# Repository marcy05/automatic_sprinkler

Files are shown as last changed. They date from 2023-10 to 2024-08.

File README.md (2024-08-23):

# Automatic Sprinkler
The project is intended to let your plant to survive while you are on holiday and you do not have any intention to buy built-in mechanism that prevent you to expand and adjust the system to your needs.

If you find this project it means that you are going to build it :)

# Getting started

## Folder Structure

The Repository is structure so that:

|Folder|Content description|
|-|-|
|/3d_files|It contans all the stl files that you need to print for the project.|
|/Board|It contains the reference schematics of the PCB|
|/Board/Production/|It contains the different files for fabrication or editing|
|/SourceCode|It contains all the developend source code|
|/SourceCode/src/ + sprinkler.py|It is the code needed for the Raspberry Pi Pico W to control the PCB board. The *src* folder has to be uploaded on the microcontroller while the *sprinkerl.py* can be executed locally for tests or uploaded on the target as well.|
|/SourceCode/Scripts/|It contains some tests that can be executed to test the wiring.|

## Bill of Material for the PCB and water buffer.

|Item #|Description|Quantity|Cost ~€/piece|Reference|
|-|-|-|-|-|
|1|Raspberry Pi Pico w|1|5,08|[Link](https://www.kubii.com/it/le-schede-raspberry-pi/3205-raspberry-pi-pico-w-h-wh-3272496311589.html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)|
|2|Multiplexer analogico CD74HC4067|2|1,30|[Link](https://www.amazon.it/gp/product/B09B4213T3/ref=ox_sc_act_title_1?smid=A2ETWJBO4PH7XN&psc=1)|
|3|Relay 3V with Optocoupler|7|3,60|[Link](https://www.amazon.it/gp/product/B07PLQNSW2/ref=ppx_yo_dt_b_search_asin_title?ie=UTF8&psc=1)|
|4|Buck converter|1|2,20|[Link](https://www.amazon.it/gp/product/B0B4S3T48P/ref=ewc_pr_img_1?smid=A1RRESHOTNJOS4&psc=1)|
|5|JST-XH 2,54mm 3pin|7|n/a|[Link](https://www.amazon.it/gp/product/B07RP6876C/ref=ppx_yo_dt_b_search_asin_title?ie=UTF8&psc=1)|
|6|JST-XH 2,54mm 2pin|7|n/a|[Link](https://www.amazon.it/gp/product/B07RP6876C/ref=ppx_yo_dt_b_search_asin_title?ie=UTF8&psc=1)|
|7|Diode IN4001|7|n/a|[Link](https://www.amazon.it/gp/product/B07Q8RPBVY/ref=ppx_yo_dt_b_search_asin_title?ie=UTF8&psc=1)|
|8|Mini water pumps 3V/5V|7|2,20|[Link](https://www.amazon.it/dp/B09Z28NFT3?psc=1&ref=ppx_yo2ov_dt_b_product_details)|
|9|Pin header connector female|Some|10|[Link](https://www.amazon.it/Headers-Breakaway-Connector-Prototype-intestazione/dp/B07CC4V9ZY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)|
|10|DC connector DC-0055.5x2.1mm|1|0,10|[Link](https://it.aliexpress.com/item/1005001688314286.html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)|
|11|Power supply 5V 2A|1|7,00|[Link](https://www.amazon.it/gp/product/B09DSWL12H/ref=ewc_pr_img_1?smid=A1LPCHZ6DX1HO3&psc=1)|
|12|Power switch 5V|1|n/a|[Link](https://www.amazon.it/gp/product/B07J4KB38W/ref=ewc_pr_img_1?smid=A3BZ3PT9ZR43MC&psc=1)|
|13|(optional) Led green|2|n/a|[Link](https://www.amazon.it/gp/product/B07DPJ23YT/ref=ewc_pr_img_1?smid=A3BZ3PT9ZR43MC&psc=1)|
|14|(optional) Box case|1|n/a|[3d_file](3d_files/case_half1.STL)|
|15|(optional) Box case cover|1|n/a|[3d_file](3d_files/case_half2.STL)|
|16|Water frame buffer|1|n/a|[3d_file](3d_files/frame_buffer.STL)|
|17|Water frame buffer top|1|n/a|[3d_file](3d_files/frame_buffer_top.STL)|
|18|Pump holders|2|n/a|[3d_file](3d_files/pump_buffer.STL)|
|19|Holder top|2|n/a|[3d_file](3d_files/holder_top.STL)|
|20|Relay support|2|n/a|[3d_file](3d_files/support_relay.STL)|
|21|(optional) PCB to be printed|1|n/a|[PCB](Board/Schematic_Automatic_Sprinkler_2023-07-30.pdf)|
|22|Empty tank sensor|1|n/a|[Link](https://www.amazon.it/dp/B0B7S2N6B3?ref=ppx_yo2ov_dt_b_product_details&th=1)|

## Software

The file must be named ***main.py*** in order to be executed directly at the start-up of the shield.

## How to start to test the softwarre

* Copy the */src* folder that you find the SourceCode folder to your Raspberry Pico W

* Copy / execute the file *sprinkler.py* . If you want that it will be executed automatically at the startup you have to copy the file *sprinkler.py* to Raspberry Pico and rename it as *main.py*

## What to do to start

1. Copy the source files in Raspberry Pi Pico W (/src + sprinkler.py)

2. Rename my_secret.py.template to my_secret.py

3. Edit my_secret.py adding:

    * Your network information (SSID, password)

    * Create a telegram bot:

        * On Telegram, search @ BotFather, send him a “/start” message

        * Send another “/newbot” message, then follow the instructions to setup a name and a username

        * Your bot is now ready, be sure to save a backup of your API token, and correct, this API token is your bot_token
    
    * Add the API token in the file

    * Save the file

4. You can now run the code

5. On Telegram, search your bot (by the username you just created), press the “Start” button or send a “/start” message

# Changelog

## V2.2.2

* Add broadcasted messages

## v2.2.1

* Add tank full control before each pump activation

## v2.2.0

* Removed direct pump activation via telegram causing issues

* Add new attribute to set back the flags for daily watering (daily_watering_done) via _watering_day

* Add new cycle to reset flags for daily watering

* Add new telegram messages for a better control on the variables in the running system

## v2.1.1

* Add support for external LEDs for RUN and WiFi

## v2.1.0

* Renamed main file for auto execution

* Add status led when running

* Set watering period to 1 day, dev 50s commented out

* Fix missing return False in is_evening

* Add flow diagrams

## v2.0.0

* First release implementing telegram controlled automatic sprinkler

* User authentication

* 7 autonomous pumps

* 7 autonomous sensors

* Automatic watering cycle

* Manual watering cycle

* Pump activation time with persistency parameters controlled remotelly

* Pump activation and deactivation with persistency and remote contol

* Emergency system stop via remote message

## v1.0.1

## v1.0.0

# Licence

Please check the dedicated file in *main* branch.

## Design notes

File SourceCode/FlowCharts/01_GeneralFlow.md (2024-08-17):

@startuml

title 01 Sprinkler General Flow

:Create HwInterface object
to reset all mux;

:Define Garden object my_garden
* Init Backend
* Init timers;

:Turn on status led;

repeat
    :my_garden.run();
repeat while (Forced exit from telegram?) is (yes)
    :Log event;
    :Reset all mux;
stop

@enduml

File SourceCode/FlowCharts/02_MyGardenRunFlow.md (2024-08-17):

@startuml

title 02 Garden Run Flow

start

if (is_tank_full() ?) then (yes)

    note right
    is_tank_full() just read the PIN 28,
    if < 3V it returns False.
    end note

    :pump_deactivation_sem = True;

    if (is_watering_moment() ?) then (yes)
        :pump_cycle();
        :watering_timer = current time;
    endif

else (no)
    if (pump_deactivation_sem) then (yes)
        :deactivate_all_pumps();
    endif

endif

if (is_sensor_reading_moment() ?) then (yes)
    :reading_sensors();
    :set sensor_reading_timer;
endif

if (is_log_moment() ?) then (yes)
    :run garbage collector;
    :log system alive;
    :get evaluate_data_from_telegram();
    if (tg answer == ForcedExit) then (yes)
        :retun "ForcedExit";
        stop
    else (no)
    endif
else (no)
endif

end

:is_watering_moment;

if (daily_watering_done) then (no)
    if (now - watering_timer >= watering_period) then (yes)
        if (NTP time sync done) then (yes)
            if (is_evening) then (yes)
                :daily_watering_done = True;
                :return True;
                stop
            else (no)
                :return False;
                stop
            endif
        else (no)
            :log NTP not sync;
            :daily_watering_done = True;
            :return True;
            stop
        endif
    else (no)
        :return False;
        stop
    endif
else (no)
    :return False;
    stop
endif

:is_evening;
: get time and date;
if (Jan, Feb, Mar, Apr, May, Oct, Nov, Dec) then (yes)
    if (current hour >= 18) then (yes)
        :retun True;
        stop
    else (no)
    endif
else (no)
endif

if (May, Jun; Jul, Sep) then (yes)
    if (current hour >= 19) then (yes)
        :return True;
        stop
    else (no)
    endif
else (no)
endif

:return False;

end

:evaluate_data_from_telegram(self);
:t_msg = telegram.read_once();

if (t_msg not None) then (yes)
    if (t_msg == "/system_stop") then (yes)
        :return ForcedExit;
        stop
    else (no)
    endif

    if (t_msg == "<general message>") then (yes)
        :<general implementation>;
        note
        The implementation depends on
        the message selected
    end note
        stop
    else (no)
    endif

else (no)
    :log no new messages;
endif

end

:pump_cycle();

repeat :for iteration in watering_iterations;
    repeat :for pump in pumps;
        if (pump get_active_status()) then (yes)
            :pump watering();
        else (no)
            :log inactive pump;
            note right
                This pump will be skipped
            end note
        endif
    repeat while (more pump?) is (yes)

repeat while (more iteration? ) is (yes)

end

@enduml

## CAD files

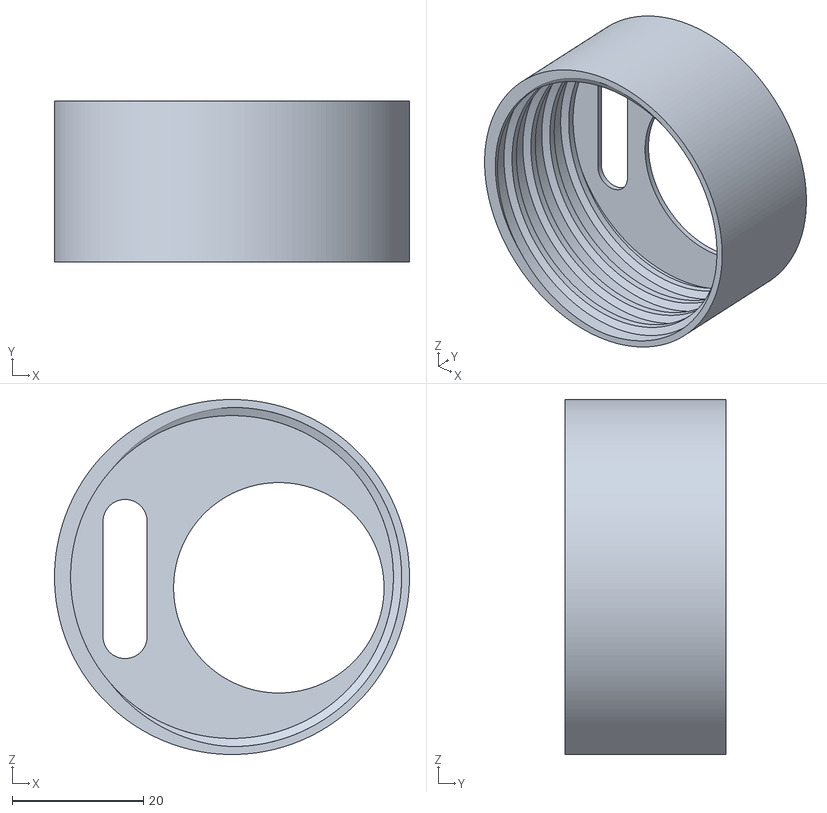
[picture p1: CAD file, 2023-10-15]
3d_files/tank_cap.STL
54.0 x 24.5 x 54.0

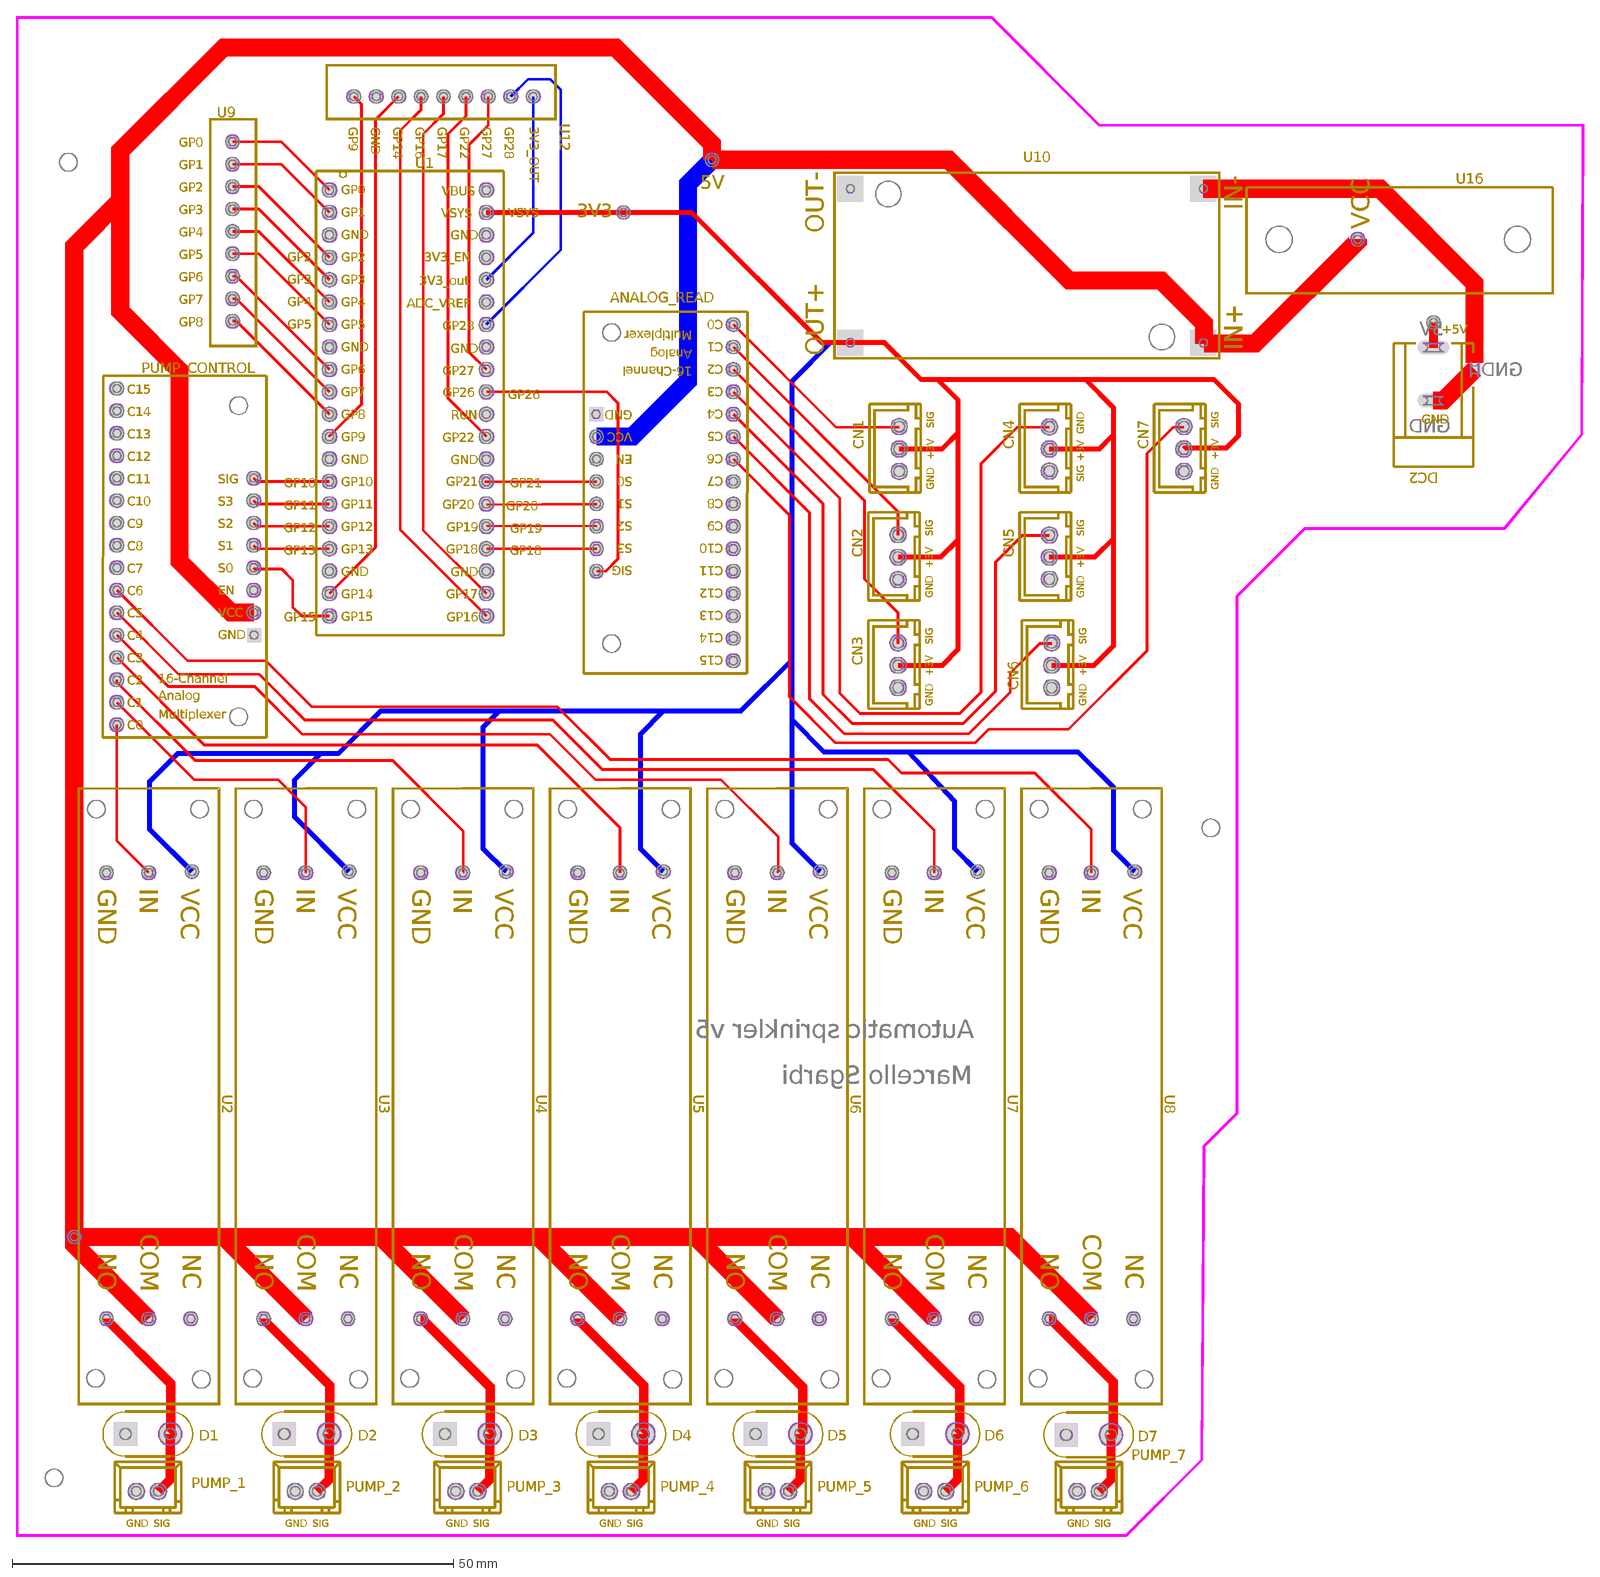
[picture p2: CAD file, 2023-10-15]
Board/Production/PCB_Irrigatore_01_2023-07-30.dxf
Automatic sprinkler v5
Marcello Sgarbi
5V
GND
+5V
3V3
GP5
GP4
GP3
GP2
GP10
GP11
GP12
GP13
GP15
GP20
GP21
GP19
GP18
GP26
VSYS
CN1
+3V
SIG
CN2
CN3
CN6
CN7
U9
GP8
GP7
GP6
GP1
GP0
U12
3V3_OUT
GP28
GP27
GP22
GP17
GP16
GP14
GP9
U16
VCC
D1
D2
D3
D4
D5
D6
D7
U10
IN+
IN-
OUT+
OUT-
DC2
CN5
CN4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

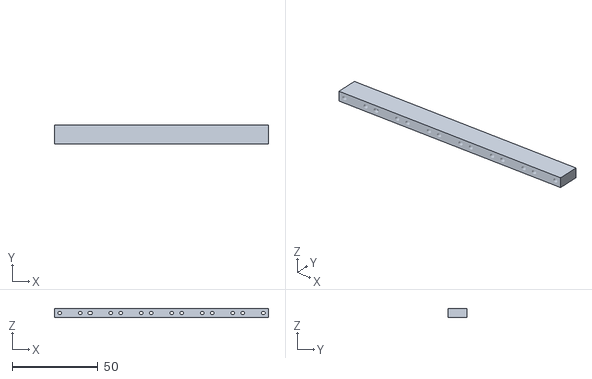
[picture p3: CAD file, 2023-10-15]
3d_files/support_relay.STL
124.8 x 11.1 x 5.00

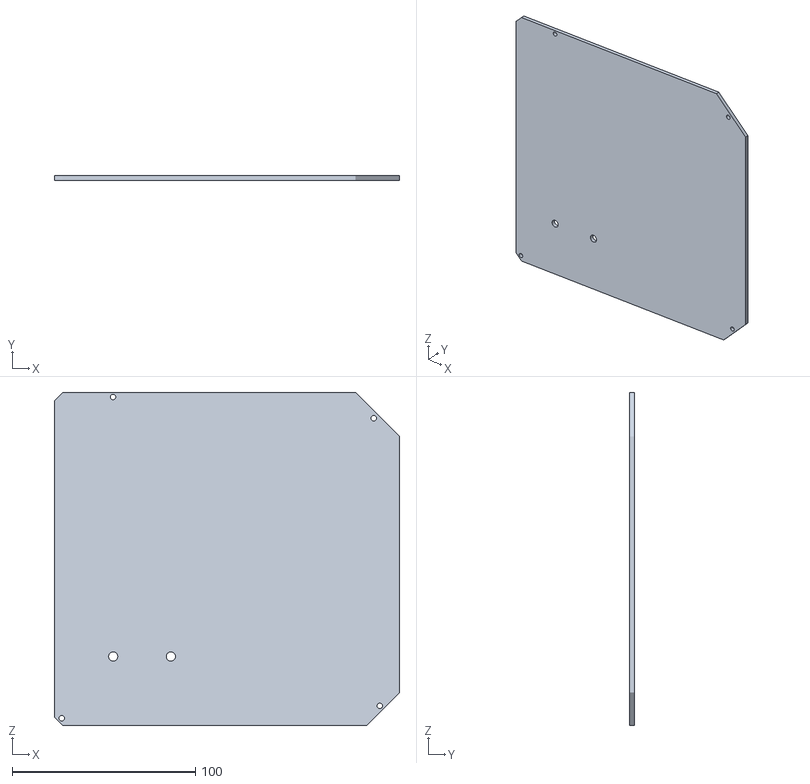
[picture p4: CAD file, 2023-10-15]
3d_files/case_half2.STL
188.4 x 2.50 x 181.9

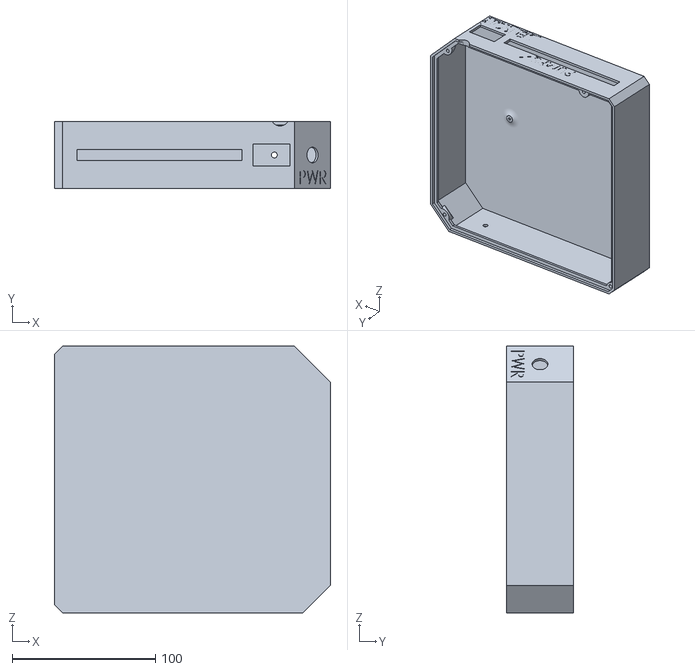
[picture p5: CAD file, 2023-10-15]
3d_files/case_half1.STL
192.4 x 47.0 x 185.9

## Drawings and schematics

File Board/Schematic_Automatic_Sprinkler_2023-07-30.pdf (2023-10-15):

## INPUT DC-DC CONVERTER LOGIC

## Extra Pins

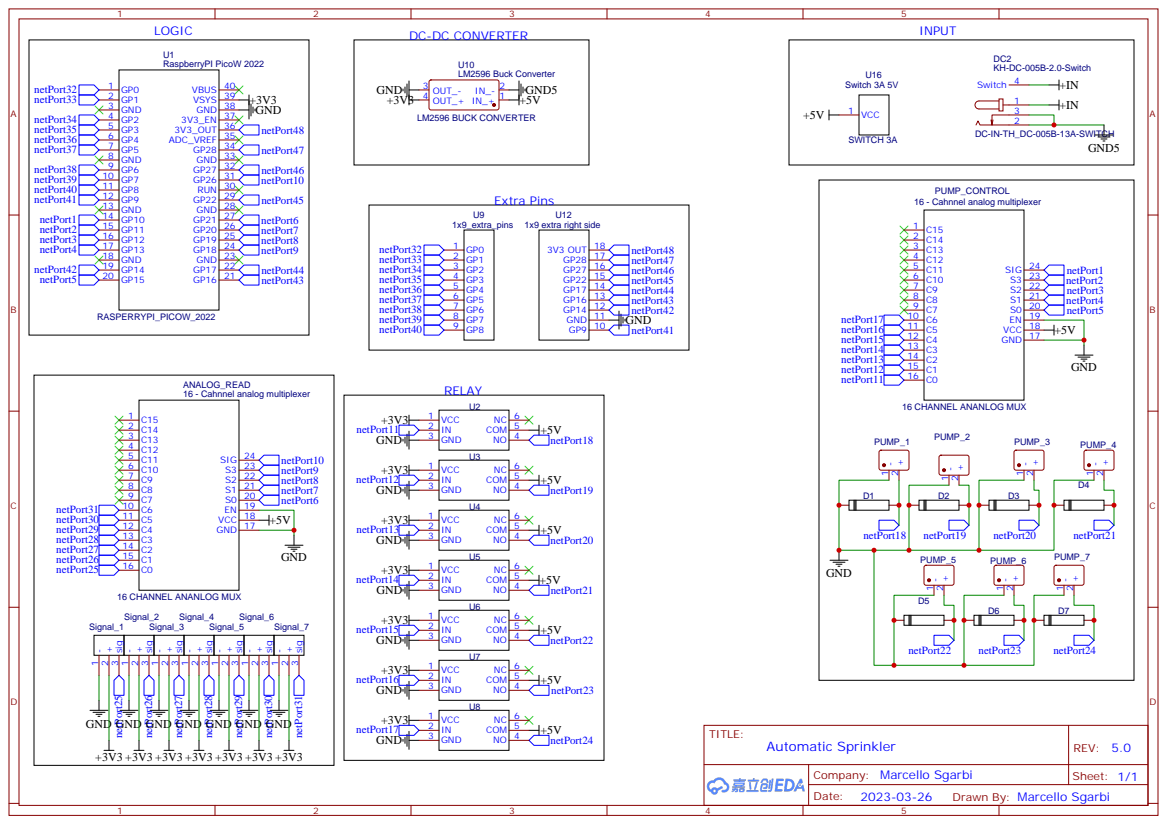
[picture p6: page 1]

ANALOG_READ
16 - Cahnnel analog multiplexer
GND 17 VCC 18 EN 19 S0 20 S1 21 S2 22 S3 23 SIG 24

netPort26
GND GND GND

Drawn By: Marcello Sgarbi

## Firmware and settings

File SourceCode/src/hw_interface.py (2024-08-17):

# #############################################################################
#                               IMPORT
# #############################################################################
import os
import utime
import machine

from src.simple_logger import logger
from src.persistencyHandler import get_persisted_timers
from src.persistencyHandler import write_persistency_value
from src.persistencyHandler import get_pump_active_status, write_pump_active_staus
from src.utils_func import bool2onoff

# #############################################################################
#                          GLOBAL VARIABLES
# #############################################################################

status_led = machine.Pin("LED", machine.Pin.OUT)
status_led.value(0)

status_led_ext = machine.Pin(9, machine.Pin.OUT)
status_led_ext.value(0)

status_led_wifi = machine.Pin(14, machine.Pin.OUT)
status_led_wifi.value(0)

# #############################################################################
#                               CLASSES
# #############################################################################

class HwInterface:
    def __init__(self) -> None:
        self.mux_channels_used = 7

        self.__pump_sig = 10
        self.__pump_s3 = 11
        self.__pump_s2 = 12
        self.__pump_s1 = 13
        self.__pump_s0 = 15

        self.__sensor_sig = 26
        self.__sensor_s3 = 18
        self.__sensor_s2 = 19
        self.__sensor_s1 = 20
        self.__sensor_s0 = 21

        self.__water_level = 28

        self.d_s0 = machine.Pin(self.__pump_s0, machine.Pin.OUT)
        self.d_s1 = machine.Pin(self.__pump_s1, machine.Pin.OUT)
        self.d_s2 = machine.Pin(self.__pump_s2, machine.Pin.OUT)
        self.d_s3 = machine.Pin(self.__pump_s3, machine.Pin.OUT)
        self.d_sig = machine.Pin(self.__pump_sig, machine.Pin.OUT)

        self.a_s0 = machine.Pin(self.__sensor_s0, machine.Pin.OUT)
        self.a_s1 = machine.Pin(self.__sensor_s1, machine.Pin.OUT)
        self.a_s2 = machine.Pin(self.__sensor_s2, machine.Pin.OUT)
        self.a_s3 = machine.Pin(self.__sensor_s3, machine.Pin.OUT)
        self.a_sig = machine.ADC(self.__sensor_sig)

        self.multiplex_selector = [(0, 0, 0, 0),
                                   (1, 0, 0, 0),
                                   (0, 1, 0, 0),
                                   (1, 1, 0, 0),
                                   (0, 0, 1, 0),
                                   (1, 0, 1, 0),
                                   (0, 1, 1, 0),
                                   (1, 1, 1, 0),
                                   (0, 0, 0, 1),
                                   (1, 0, 0, 1),
                                   (0, 1, 0, 1),
                                   (1, 1, 0, 1),
                                   (0, 0, 1, 1),
                                   (1, 0, 1, 1),
                                   (0, 1, 1, 1),
                                   (1, 1, 1, 1)]

        self.water_level = machine.ADC(self.__water_level)

    def reset_digital_mux(self):
        logger.debug(f"{self.__class__.__name__} - Start resetting all relays...")
        for channel in range(self.mux_channels_used):
            self.d_s0.value(self.multiplex_selector[channel][0])
            self.d_s1.value(self.multiplex_selector[channel][1])
            self.d_s2.value(self.multiplex_selector[channel][2])
            self.d_s3.value(self.multiplex_selector[channel][3])
            self.d_sig.value(False)
        logger.info(f"{self.__class__.__name__} - Reset relays done.")

    def set_channel_value(self, channel: int, signal: bool):
        logger.debug(f"{self.__class__.__name__} - Channel: {channel} with Value: {signal}")
        self.d_s0.value(self.multiplex_selector[channel][0])
        self.d_s1.value(self.multiplex_selector[channel][1])
        self.d_s2.value(self.multiplex_selector[channel][2])
        self.d_s3.value(self.multiplex_selector[channel][3])
        self.d_sig.value(signal)

    def _read_u16(self, adc_read: int) -> float:
        """
        Convert the Vdigit to Volt value from ADC.
        """
        return adc_read * 3.3 / 65535

    def get_analog_from_mux(self, channel: int) -> float:
        logger.debug(f"{self.__class__.__name__} - Channel: {channel} reading...")
        self.a_s0.value(self.multiplex_selector[channel][0])
        self.a_s1.value(self.multiplex_selector[channel][1])
        self.a_s2.value(self.multiplex_selector[channel][2])
        self.a_s3.value(self.multiplex_selector[channel][3])
        volt = self._read_u16(self.a_sig.read_u16())
        return volt

    def get_water_sensor_voltage(self) -> float:
        volt = self._read_u16(self.water_level.read_u16())
        return volt
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

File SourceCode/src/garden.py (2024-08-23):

# #############################################################################
#                               IMPORT
# #############################################################################
import gc
import utime

import src.const as const

from src.simple_logger import logger
from src.hw_interface import Sensor, Pump, WaterLevel
from src.backend import BackEndInterface
from src.backend import TelegramMessage
from src.persistencyHandler import get_int_from_json, get_float_from_json
from src.persistencyHandler import write_persistency_value
from src.utils_func import status2bool, bool2onoff
from src.utils_func import forced_exit_txt, get_time

# #############################################################################
#                               CLASSES
# #############################################################################


class Garden:
    def __init__(self) -> None:
        logger.info(f"{self.__class__.__name__} - Init Gerden...")

        self._timers_persistency_path = "src/timers.json"

        self.start_time = utime.time()

        self.watering_timer = utime.time()
        self.daily_watering_done = False
        self._watering_day = 0
        self._watering_verification_period = 600  # Verify each 10min
        # self._watering_verification_period = 60  # erase this for real application
        self.watering_iterations = get_int_from_json("garden_watering_iteration", self._timers_persistency_path)
        utime.sleep(1)
        self.watering_itersations_delay = get_int_from_json("garden_water_iteration_delay", self._timers_persistency_path)  # seconds of delays between one watering action and another.

        self.back_sync_timer = utime.time()
        self.back_sync_period = get_int_from_json("backend_sync_period", self._timers_persistency_path)  # Period of time for backend sync in seconds

        self.sensor_reading_timer = utime.time()
        self.sensor_reading_period = get_int_from_json("sensor_reading_period", self._timers_persistency_path)  # Sensor reading period in seconds

        self.log_bit_timer = utime.time()
        self.log_bit_period = 2  # Log heartbit in seconds
        logger.debug(f"{self.__class__.__name__} - [ok] timers and period initialized")

        self._day_pass_timer = utime.time()
        self._day_pass_persiod = 600  # Check each 10min

        logger.debug(f"{self.__class__.__name__} - Initializing pumps and sensors...")
        self.pumps = [Pump(i) for i in range(7)]
        self.sensors = [Sensor(i) for i in range(7)]
        self._tank_level = WaterLevel()
        self._pump_deactivation_sem = False

        logger.debug(f"{self.__class__.__name__} - [ok] pumps and sensors initialized")

        self.backend = BackEndInterface()
        logger.debug(f"{self.__class__.__name__} - [ok] backend initialized")

        logger.info(f"{self.__class__.__name__} - [ok] Init completed.")

        self._sem_tank_full_bot = True

    def init_timers(self):
        # This functions allows to sync all timers after that the NTP sync
        #   has properly set the RTC time.
        init_time = utime.time()
        self.start_time = init_time
        self.watering_timer = init_time
        self.back_sync_timer = init_time
        self.sensor_reading_timer = init_time
        self.log_bit_timer = init_time
        self._day_pass_timer = init_time

    def _is_evening(self):
        tm = utime.localtime()
        month = tm[1]
        hour = tm[3]
        # Consider evening erlier in colder months
        if (month >= 1 and month <= 5) or (month >= 10 and month <= 12):
            if hour >= 18:
                return True
        # Consider evening late in hotter months
        if month > 5 and month < 10:
            if hour >= 19:
                return True
        return False

    def is_tank_full(self) -> bool:
        if self._tank_level.is_tank_full():
            self._sem_tank_full_bot = True
            return True
        else:
            if self._sem_tank_full_bot:
                self.backend.tg_broadcast("Tank is empty.")
                self._sem_tank_full_bot = False
            return False

    def _deactivate_all_pumps(self) -> None:
        logger.info(f"{self.__class__.__name__} - Deactivating all pumps...")
        for pump in self.pumps:
            pump.set_status(False)
        logger.info(f"{self.__class__.__name__} - All pumps deactivated")

    def __monitor_watering_day(self):
        current_day = utime.localtime()[2]
        if self._watering_day != current_day:
            self.daily_watering_done = False
            logger.info(f"Set missing watering for the day. Last: {current_day}; Current: {self._watering_day}")
        # else:
        #     logger.debug(f'Current date {current_day} == Last watering {self._watering_day}')

    def is_watering_moment(self):
        if not self.daily_watering_done:
            if (utime.time() - self.watering_timer) >= self._watering_verification_period:
                if self.backend.ntp_sync_done:
                    if self._is_evening():
                        self.daily_watering_done = True
                        self._watering_day = utime.localtime()[2]
                        return True
                    else:
                        return False
                else:
                    logger.debug(f"{self.__class__.__name__} - NTP not sync. Watering timeout expired.")
                    self.daily_watering_done = True
                    self._watering_day = utime.localtime()[2]
                    return True
            return False
        return False

    def pump_cycle(self):
        self.backend.tg_broadcast("Start watering cycle")
        for iteration in range(self.watering_iterations):
            logger.debug(f"{self.__class__.__name__} - Watering iteration: {iteration + 1}/{self.watering_iterations}")
            for pump in self.pumps:
                if pump.get_active_status():
                    if self.is_tank_full():
                        pump.watering()
                    else:
                        logger.warning("The tank is empty")
                else:
                    logger.debug(f"The pump:{pump.pump_id} has Active status to False. It will be skipped")
            utime.sleep(self.watering_itersations_delay)
        self.backend.tg_broadcast("Watering cycle completed")

    def is_backend_sync_moment(self):
        if (utime.time() - self.back_sync_timer) >= self.back_sync_period:
            logger.debug(f"{self.__class__.__name__} - Backend sync time")
            return True
        return False

    def _get_sensors_data(self) -> str:
        sensors_data = ""
        for sensor in self.sensors:
            sensors_data += f"{sensor.get_str_data()}\n\n"
        return sensors_data

    def _get_pumps_data(self) -> str:
        pumps_data = ""
        for pump in self.pumps:
            pumps_data += f"{pump.get_str_data()}\n\n"
        return pumps_data
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

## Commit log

2022-09-07 moved time print when 1min or 1day is passed
2022-09-07 Changed timer to better identify that when in sleep the water is flowing
2022-09-07 added function to ensure that the relais are switched off and avoid that the last one remains active
2022-09-07 Removed and added print statements
2022-09-07 Removed not used init for analog mux. No init value for ADC
2023-01-14 Modified pinout to match board v2
2023-01-14 Added schematic and board prduction files
    [Sprinkler_v3_20221229.pcbdoc]
2023-01-14 Added 3D files for switch support and pumps support
    [holder_side.STL, holder_top.STL, interruttore.STL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]
2023-02-04 Created frame enclousure for pump buffer
    [frame.STL, switch_holder.STL, top_frame.STL]
2023-02-04 Remamend interruttore.STL to switch_holder.STL
    [interruttore.STL]
2023-02-04 Added test script to test all the sensors
2023-02-05 Added files to test the board and have a feedback on sensors
2023-02-06 Added tests scripts to check the correct reading from the board
2023-02-06 Added class to track the sensor and function to convert from ADC volto to real volt
2023-02-06 Added class to handle the sensors and init the active and inactive one
2023-02-13 Improved script to test sensors
2023-02-19 Board v4 schematics and production updated
    [PCB_Irrigatore_01_2023-02-19.dxf, Sprinkler_v3_20221229.pcbdoc]
2023-02-19 Overall loop works with respect to timers. To be tested with water and plants to set the thresholds
2023-03-04 New samples with the mqtt client and internet connection working
2023-03-25 excluded easy connection to raspberry
2023-03-25 Added Pump class and HwInterface
2023-03-25 Added Sensor to the handling
2023-03-29 Modified timers for main loop tests
2023-03-29 Adding execution flow chart
2023-04-01 Updated files for V5 board review
    [PCB_Irrigatore_01_2023-02-19.dxf]
2023-04-01 Chaged default value for Pump and Sensor
2023-04-01 Added libraries and secret structure to be filled before copying it to the raspberry
2023-04-06 Updated flow chart
2023-04-06 Start adding description for Raspberry Pi 2 set up
2023-04-11 updated switch handler 3d File to add OFF comment
    [switch_holder.STL]
2023-04-19 Added new file for subscriber implementation on raspberry
2023-04-19 Added logging instead of printing
2023-04-25 Added test for pump tests
2023-04-25 Mqtt publishing pump sensor to the defided topic
2023-05-01 Data should be inserted in UTC time
2023-05-14 Added STL file for support for rele
    [support_rele.STL]
2023-05-17 Fixed varaible initialization and fixed animation for too much current absorbed
2023-05-17 Push button control verified
2023-05-28 renamed class from Pump to Button
2023-05-28 Evaluating push button pressing and send communication via mqtt
2023-06-17 Added retry connection in case of failed connection.
2023-06-17 Added multi thread led handling for initialization
2023-06-17 Added box case for board
    [case_half1.STL, case_half2.STL]
2023-07-17 updated box files
    [case_half1.STL, case_half2.STL]
2023-07-29 Reorganized files and removed timers not needed
2023-07-30 Created BOM and updated Readme file
    [PCB_Irrigatore_01_2023-07-30.dxf, PCB_Irrigatore_01_2023-07-30.pcbdoc, frame_buffer.STL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]
2023-07-30 Added missing switch
2023-08-06 Updated frame buffer
2023-08-07 Updated hole size
2023-08-13 Added water level sensor reading
2023-08-13 Deactivated all pumps tank is emptly
2023-08-13 Add warning log level because water sensor not calibrated
2023-10-11 Added persistency timers and inteface
2023-10-14 Garden timers and settings paratetrized in config
2023-10-14 Removed log warning for level sensor, no more valid
2023-10-14 Fixed bug in pump deactivation for empty tank
    [garden.py, hw_interface.py]
2023-10-14 Changed log level for pump deactivation
2023-10-14 Fixed bug. Avoid that pumps are deactivated in each bus cycle
    [garden.py]
2023-10-15 Rebasing after feature/short_port_timeout merging
    [backend.py, garden.py, hw_interface.py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]
2023-10-15 Add log message in case a pump has Active staus to off
2023-10-15 Retrieving pump activation status implemented
2023-10-15 Switched all status from bool to on off support and improved start message
2023-10-15 Reset pumps before exiting the cycle when forcing the exit
2023-10-15 Removed not used 3D parts
    [holder_top.STL, pump_buffer.STL, switch_holder.STL]
2023-10-15 add tank cap 3D model
    [tank_cap.STL]
2023-10-15 Updated Readme and added missed untracked file secretHandler.py
    [secretHandler.py]
2024-08-17 Add status led to show running system
2024-08-17 Fixed missing return False in is_evening
    [garden.py]
2024-08-17 Add flow diagrams
2024-08-17 Add handling of external LEDs
2024-08-19 Removed tg set to directly activate pump. Issues.
    [backend.py]
2024-08-19 New release ready. Improved behaviors and fixed issues
    [backend.py, garden.py, persistencyHandler.py]
2024-08-19 Updated readme for a new release
    ## v2.2.0
    * Removed direct pump activation via telegram causing issues
    * Add new attribute to set back the flags for daily watering (daily_watering_done) via _watering_day
    * Add new cycle to reset flags for daily watering
    * Add new telegram messages for a better control on the variables in the running system
